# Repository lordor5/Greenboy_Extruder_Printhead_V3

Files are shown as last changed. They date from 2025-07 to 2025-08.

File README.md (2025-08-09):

# Greenboy_Extruder_Printhead_V3
An Alternative Printhead design for the Greenboy Pellet extruder

This toolhead brings many quality of life improvements like removable pellet hose connetor, easier assembly, more compact design, minimal disassembly required to pull the screw which can be performed with the printhead still attached to the printer and similar improvements.

As this design uses a seperate mounting plate between the printer and the printhead you only need to edit that to use it on a not yet supported printer, same with using another z probe for which there are 3 mounting holes in the mounting plate.

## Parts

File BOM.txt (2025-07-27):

Mandatory:

---------------------------------------------

Main body: 			4x m3x50
				4x m3 hexnut
		
Part cooling fan:		2x m3x18-20

Part cooling fan duct:		2x m3x6-10
				2x m3x6-10

Hotend cooling fan:		2x m3x18-20

Hotend cooling fan duct:	2x m3x6-10	

Mounting plate: 		3x m3x10
				3x m3 hexnut
---------------------------------------------

Mounting plate to printer:

---------------------------------------------

Ender 3:			2x m3x8

---------------------------------------------

Optional:

---------------------------------------------

Front bucket lid:		2x m3x8
				2x m3 hexnut

Z probe adapter BL-touch:	3x m3x8
				2x m3x6
				5x hexnut

Z probe adapter cartographer:	3x m3x10
	same as beacon rev-D	2x m3x8
				1x m3x20-25
				5x hexnut

---------------------------------------------

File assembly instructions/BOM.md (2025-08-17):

# Mandatory:

| Section | Fastener Type | Quantity |
| --- | --- | --- |
| **Main body** | m3x50 | 4 |
| | m3 hexnut | 4 |
| **Hotend fixture** | m4x8-12 | 4 |
| **Part cooling fan** | m3x18-20 | 2 |
| **Part cooling fan duct** | m3x6-10 | 4 |
| **Hotend cooling fan** | m3x18-20 | 2 |
| **Hotend cooling fan duct** | m3x6-10 | 2 |
| **Mounting plate** | m3x10 | 3 |
| | m3x8 | 2 |
| | m3 hexnut | 3 |
| | m3 7mm OD shims | 3 |
| **Front bucket lid** | m3x8 | 2 |
| | m3 hexnut | 2 |

---------------------------------------------

# Mounting plate to printer:

| Section | Fastener Type | Quantity |
| --- | --- | --- |
| Ender 3 | m3x8 | 2 |

---------------------------------------------

# Optional:

|Section|Fastener Type|Quantity|Notes|
|---|---|---|---|
|**Z probe adapter BL-touch**|m3x8|3||
||m3x6|2||
||hexnut|5||
|**Z probe adapter cartographer**|m3x10|3|Same as Beacon Rev-D|
||m3x8|2||
||m3x20-25|1||
||hexnut|5||

---------------------------------------------

If you notice any issues with this guide, have any questions or need clarifications
please contact me, preferably in the Greenboy3D discord @alx1234 or alternatively via email at alx.3dp@gmail.com

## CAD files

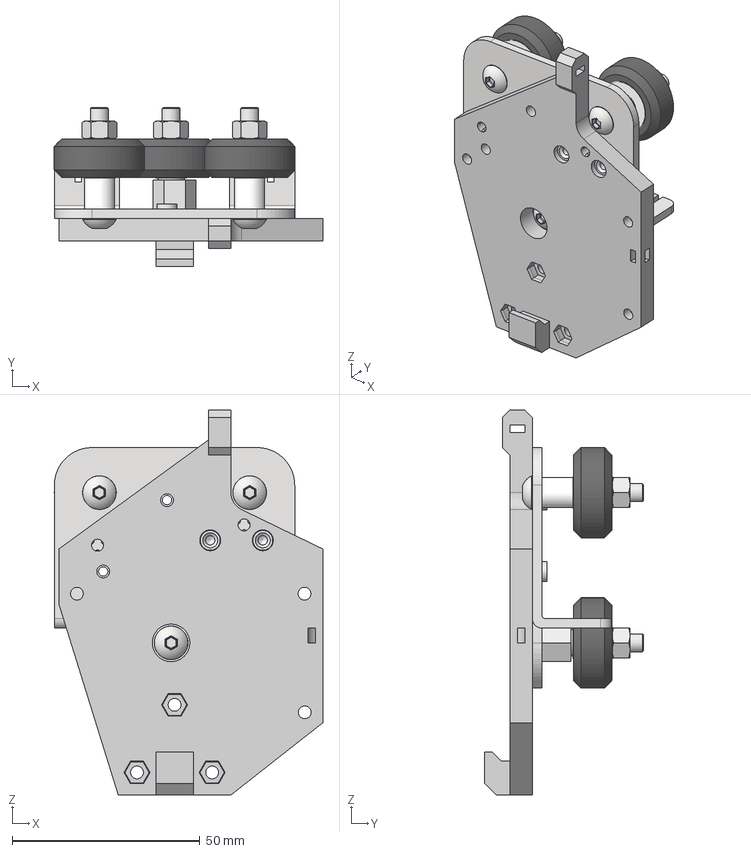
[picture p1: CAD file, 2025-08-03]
step/Mounting plates/Ender 3/Ender3 printer mounting plate.step
71.5 x 42.2 x 102.5 mm
Основание_3
AS 1112 - M5 Тип 5 x 3
Винт_1 x 3
Ролик_1 x 3
Эксцентрик
Дистанционная_ втулка x 2
GB printhead V3

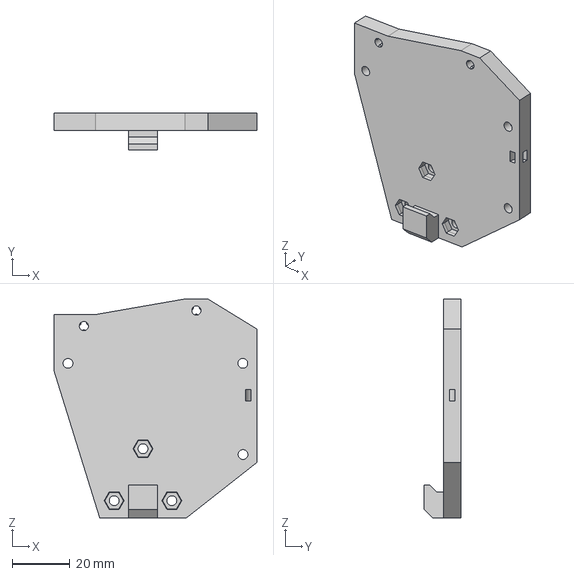
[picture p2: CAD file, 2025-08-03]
step/Mounting plates/mounting plate base.step
70.3 x 12.7 x 75.9 mm

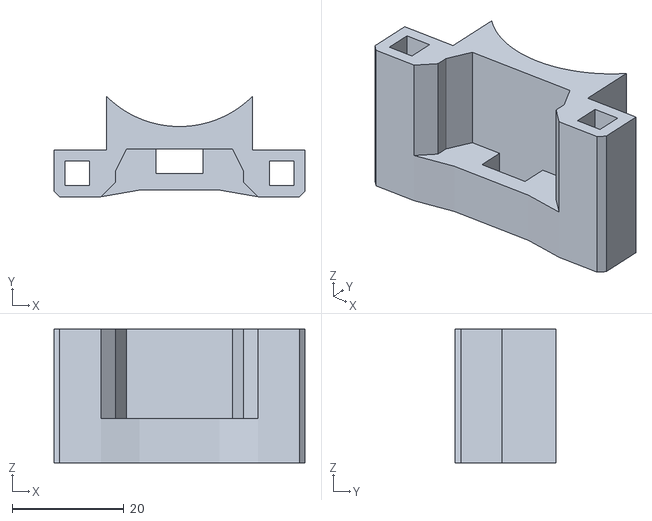
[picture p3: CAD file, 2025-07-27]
stl/alternate front/wall front.stl
45.0 x 18.0 x 24.0

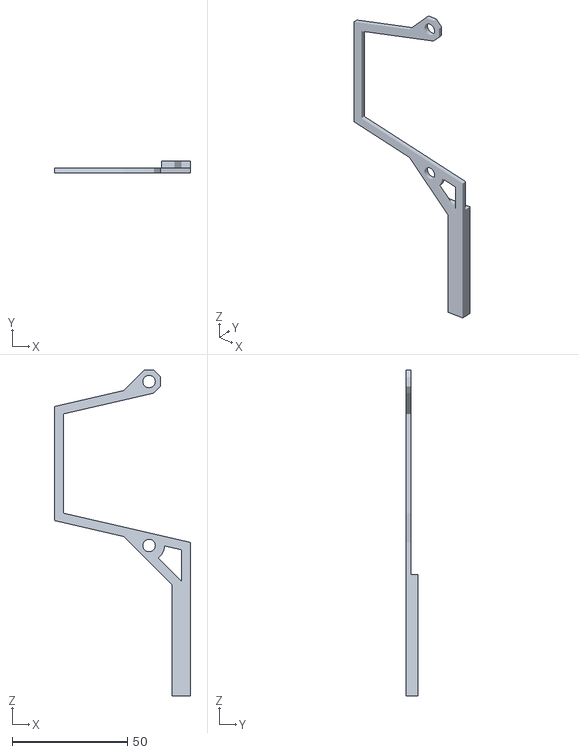
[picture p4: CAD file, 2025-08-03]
stl/Mounting plates/Ender 3/z limit switch extension.stl
59.0 x 5.00 x 141.1

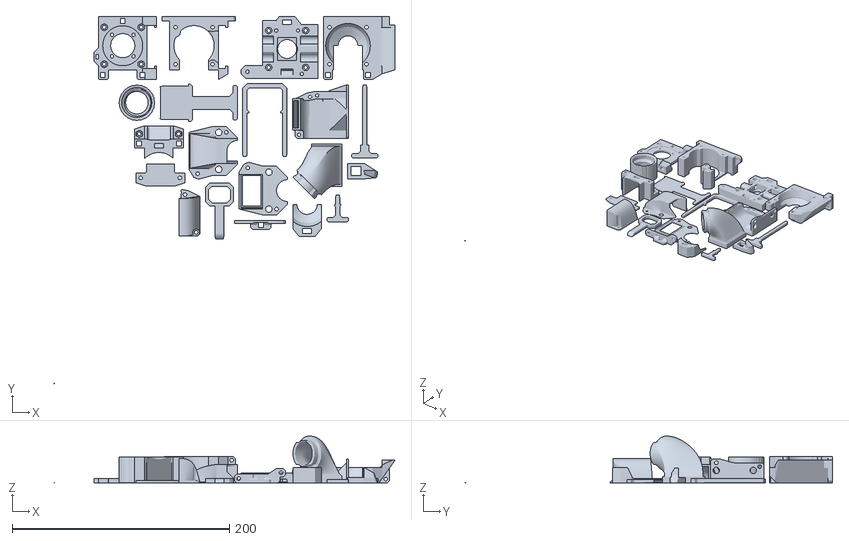
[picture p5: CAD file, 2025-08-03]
stl/Printhead all parts.stl
313.4 x 337.6 x 43.0

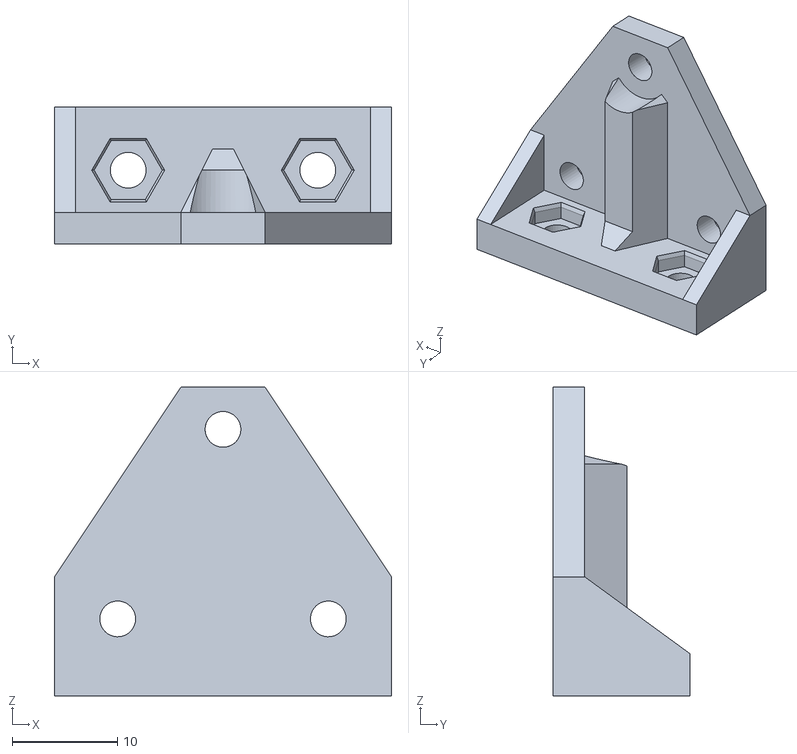
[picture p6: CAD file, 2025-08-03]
stl/z probe mounts/Bl touch mount.stl
32.0 x 13.0 x 29.3

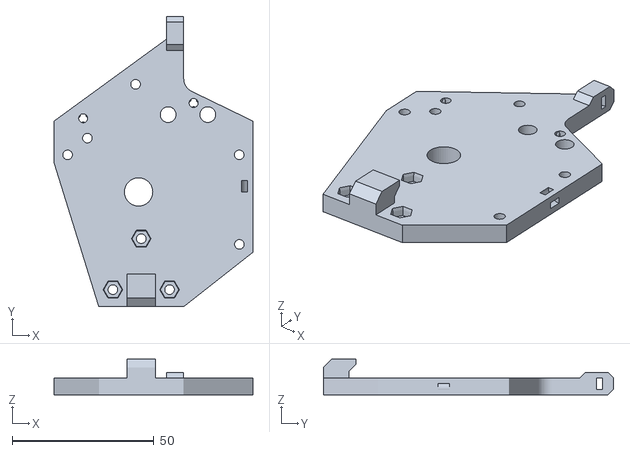
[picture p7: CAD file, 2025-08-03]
stl/Mounting plates/Ender 3/mounting plate Ender 3.stl
70.3 x 102.5 x 12.7

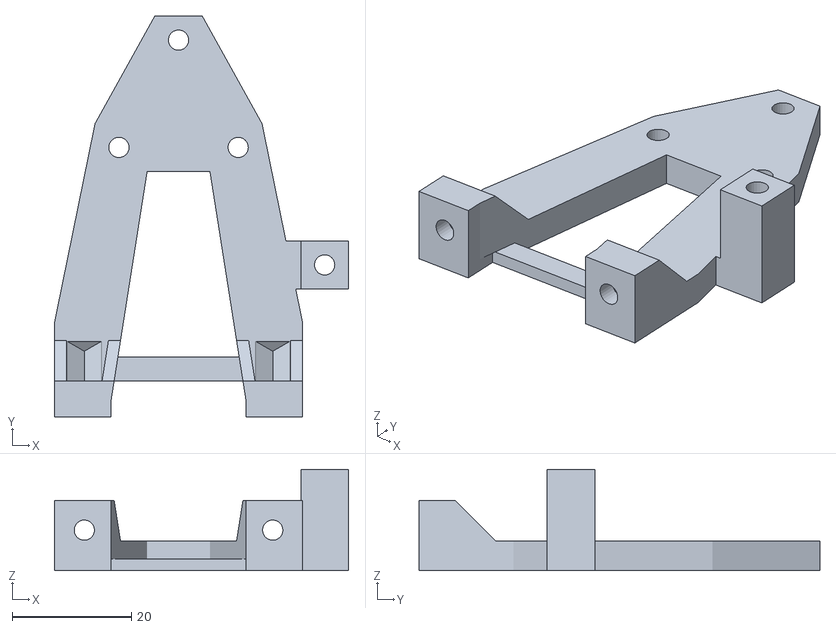
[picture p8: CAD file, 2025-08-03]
stl/z probe mounts/cartographer mount.stl
49.3 x 67.2 x 17.0

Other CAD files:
step/Mounting plates/Ender 3/Ender 3 z limit switch extension.step

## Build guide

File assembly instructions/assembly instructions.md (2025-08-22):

# Preparation:

Remove the old toolhead from the printer.

Use a m3 screw to drag the m3 hex nuts into their fixtures.
If you do not use a z probe you do not need the 3 bottom ones in the mounting plate

Assemble the Hotend by inserting the heater and thermistor into the heating block.
Screw the Heating block onto the Extruder barrel. If it is at a weird angle you can turn it around ans crew it on the other way. If the grub screws need to be on the bottom to have it align properly you can cut a bit of the insulation of the thermistor away to push it in further. Be careful not to cut the wires though.
You can screw in the nozzle at this point though that can also be done once its fully assembled.

Press the Inlet Rotor on top of the Pellet screw as far down as possible.
Make sure it is aligned right next to the inlet.
After that you can already put the coupler on the screw and tighten it down as much as possible.
I suggest getting some torx screws to allow better tightening without stripping the screw.
The coupler uses m2.5x8 screws.

Press the Pellet hose connector on the pellet hose adapter.
If your pellet hose is already the correct size you can also screw the pellet hose connector on it already, but you can also wait till the whole printhead is assembled.

# Assembly:

You can use the pictures in the pics folder for reference.

1. **Step one:** Screw the Motor plate to the Motor with 4 m3x6-8 screws.
Make sure you have the motor oriented the way you want it as you will not be able to chnage this later.

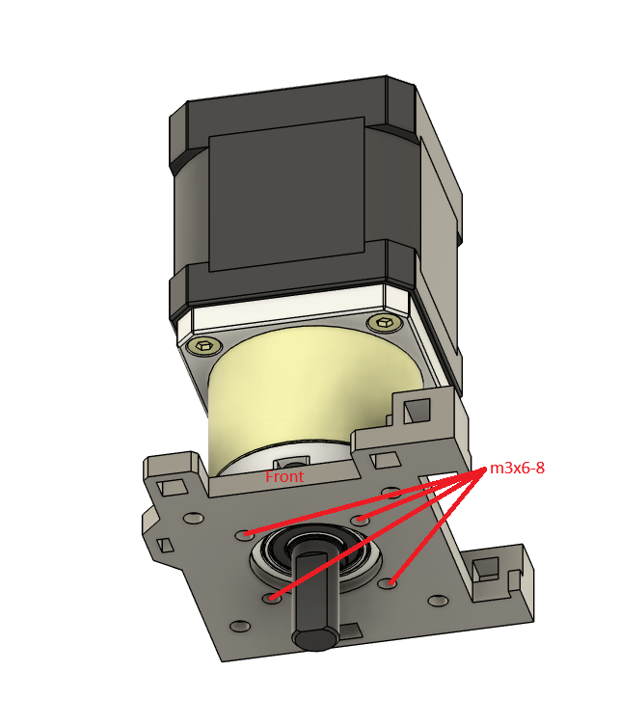
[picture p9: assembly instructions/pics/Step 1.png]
Step 1.png


2. **Step two:** Screw the Hotend Barrel into the Hotend fixture with 4 m4x8-12 screws.
Make sure the heating block is pointing backwards.
You might need to screpe a bit of material out of the printed part to fit the hotend properly.
Look through the holes of the Fixture to lighn the holes upproperly.
Be carful when screwing the scrws in to make sure everything is aligned properly so that you do not damage the threads of the Barrel.

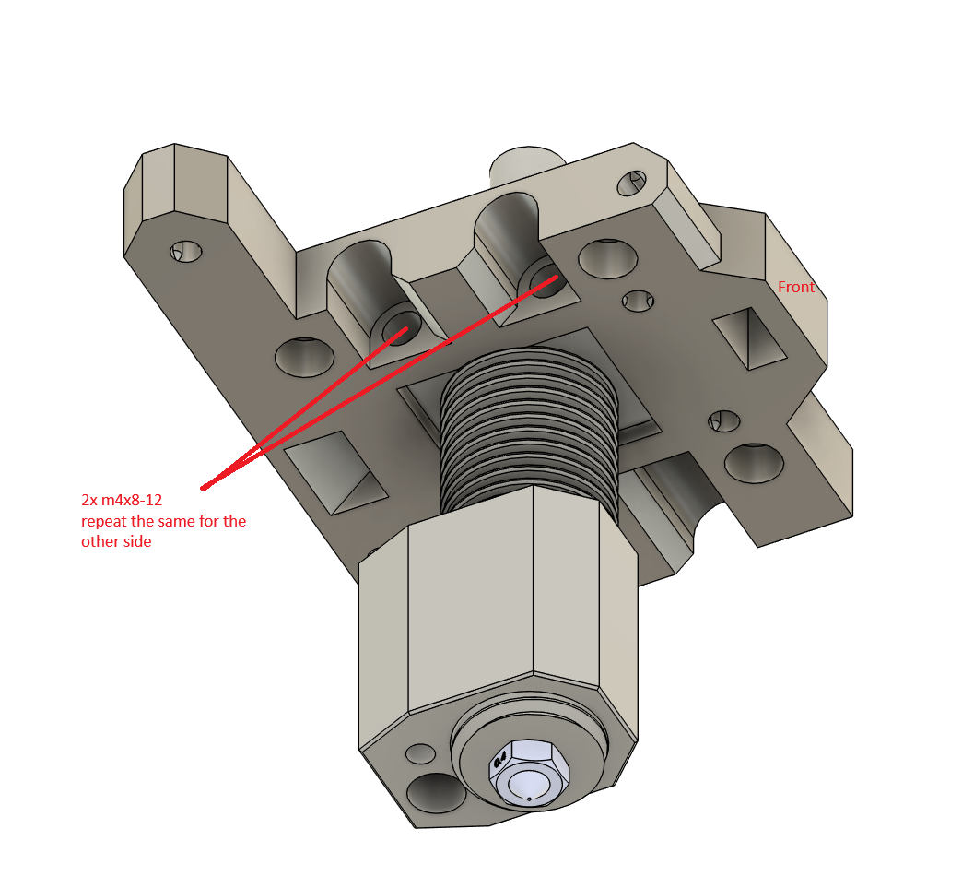
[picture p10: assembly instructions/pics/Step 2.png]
Step 2.png


3. **Step three:** Put the pellet screw in the hotend barrel. You need to have the rotor facing the front for this.
Use 4 m3x50 screws to connect the hotend fixture to the funnel,
pellet reservoir and motor plate and tighten them down.
Tighten the motor side of the coupler as much as you can, as said earlier.
I recommend getting torx screws to not have an issue with stripping them.

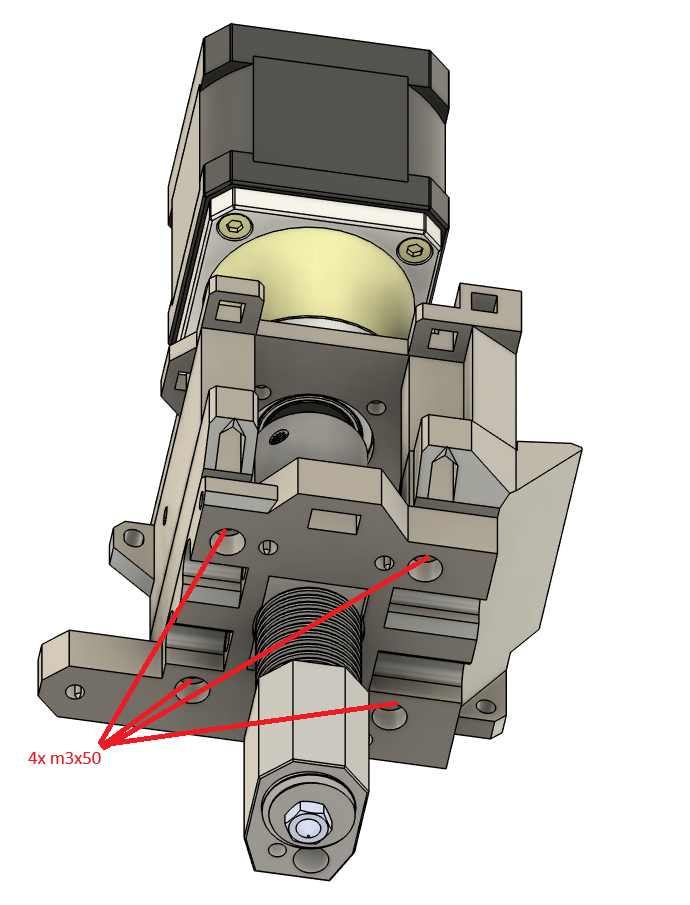
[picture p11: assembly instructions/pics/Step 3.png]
Step 3.png


4. **Step four:** Use 2 m3x18-20 screws to moun theHotend fan to the left side of the printhead.

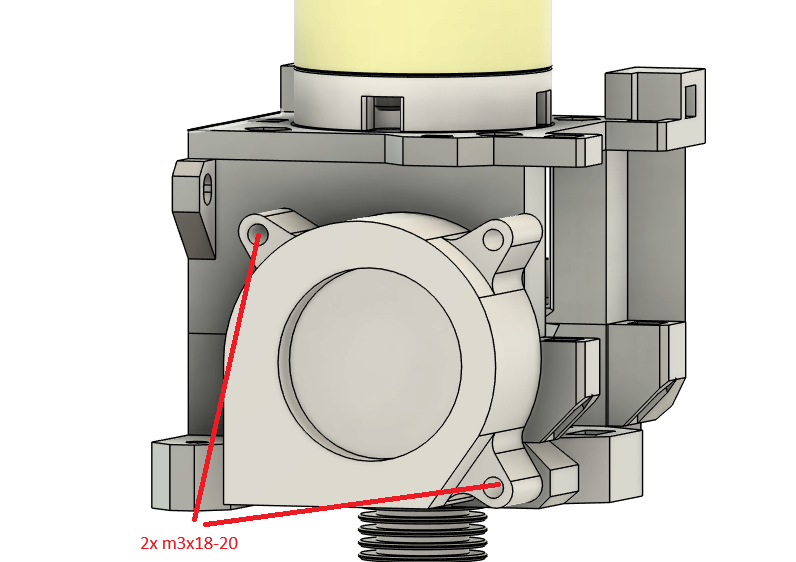
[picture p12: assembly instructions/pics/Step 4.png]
Step 4.png


5. **Step five:** Mount the 2 parts of the hotend cooling duct to the Printhead using 2 m3x6-10 screws.

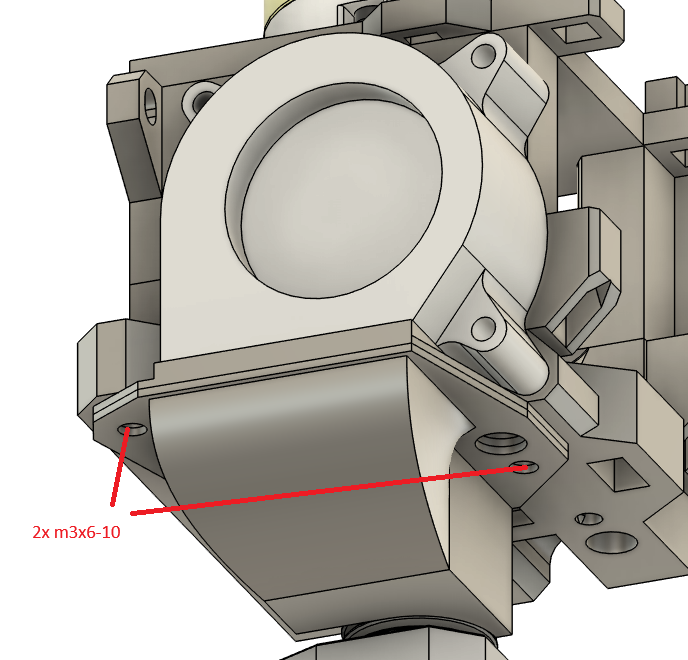
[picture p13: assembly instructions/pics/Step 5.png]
Step 5.png


6. **Step six:** Connect the 2 parts of the Part cooling duct with 2 m3x6-10 screws

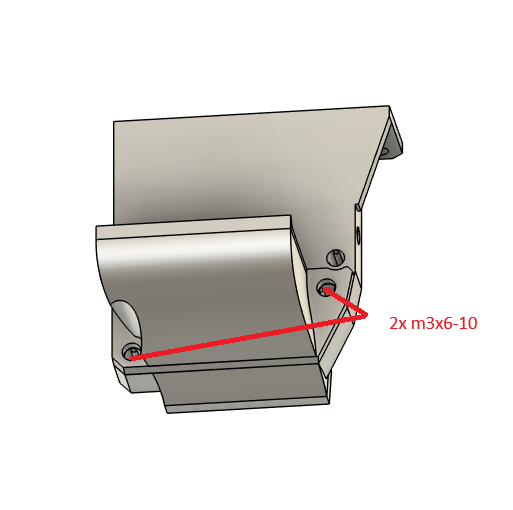
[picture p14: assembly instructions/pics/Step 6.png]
Step 6.png


7. **Step seven:** Mount the part cooling duct on the printhead woth 2 m3x6-10 screws.

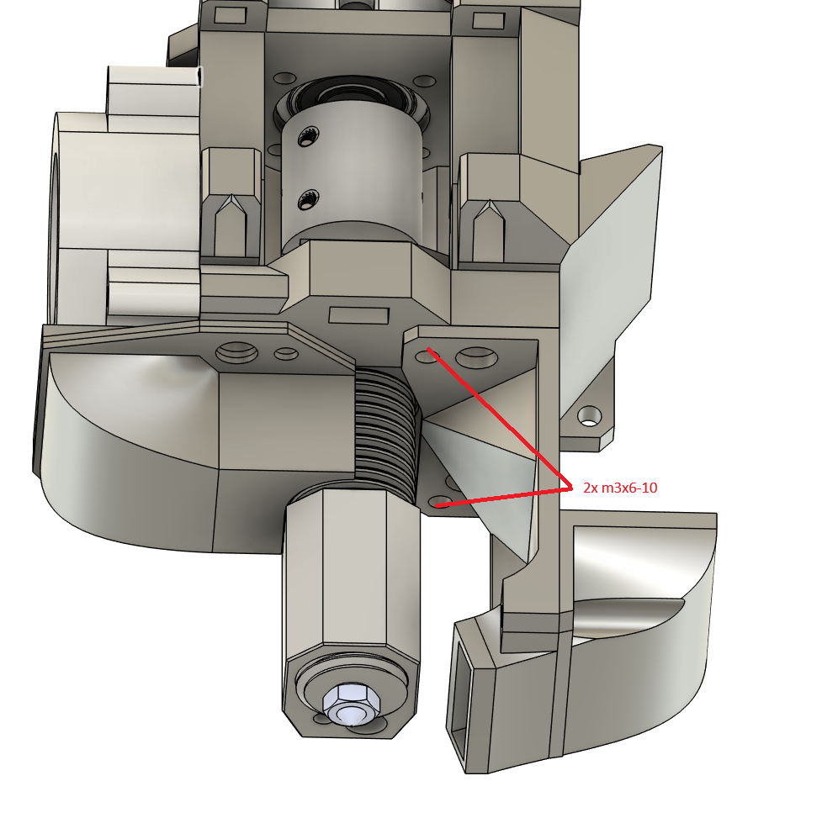
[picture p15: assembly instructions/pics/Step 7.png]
Step 7.png


8. **Step eight:** Screw the part cooling fan to the Printhead with 3 m3x18-20 screws.

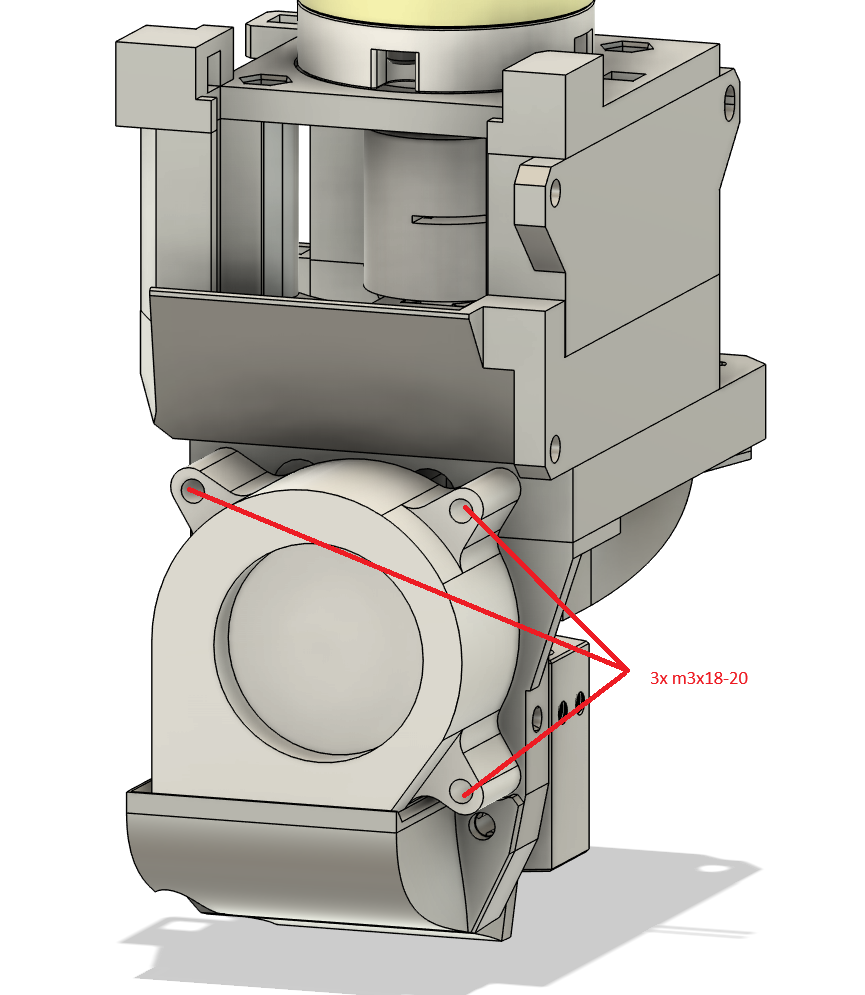
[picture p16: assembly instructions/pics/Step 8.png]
Step 8.png


9. **Step nine:** Screw the back latch fixture to the mounting plate with 2 m3x8 srew

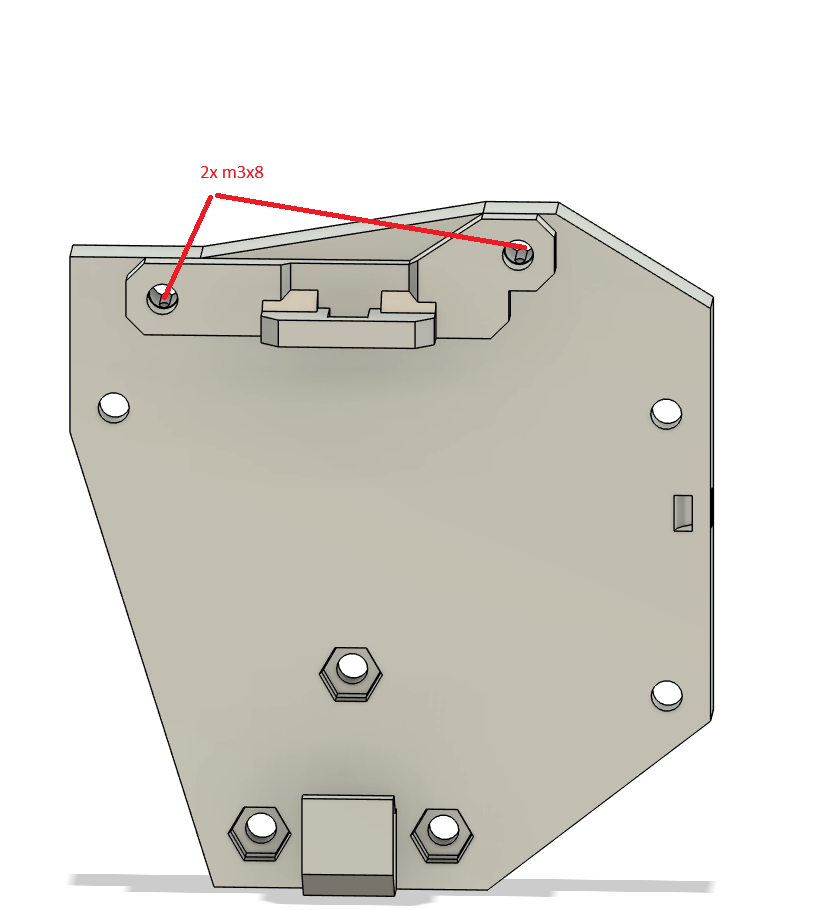
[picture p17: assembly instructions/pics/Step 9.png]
Step 9.png


10. **Step ten:** If you are using a z probe mount the Z-probe to the Z-probe mount and screw it to the mounting plate.
There are different screws used for this, consult the BOM to find out wich ones you need.

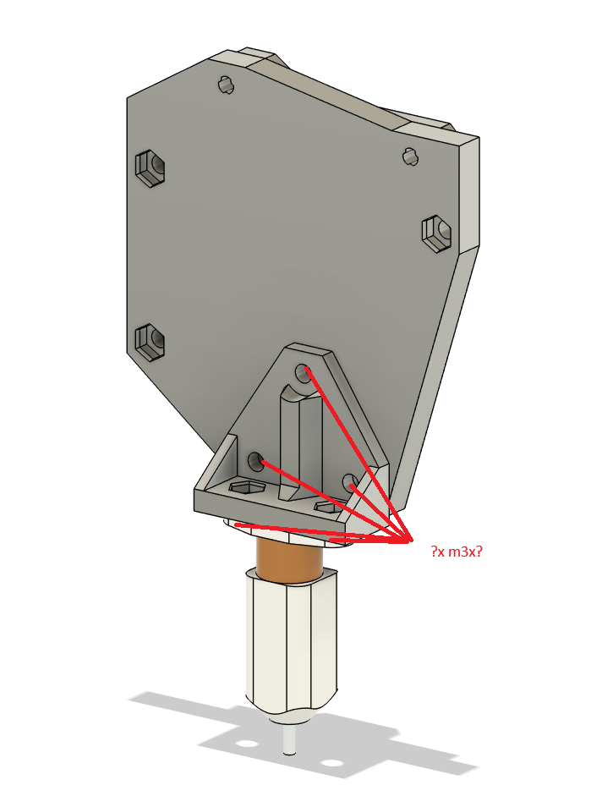
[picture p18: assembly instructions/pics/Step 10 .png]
Step 10.png


11. **Step eleven:** Mount the Mounting plate to the printhead.
Depending on your printer this needs different screws, consult the BOM for this.

12. **Step twelve:** Mount the printhead to the mounting plate.
Set it on the bottom hook first and then rotate it back flat onto the mounting plate.
secure it in theis position with the back latch.

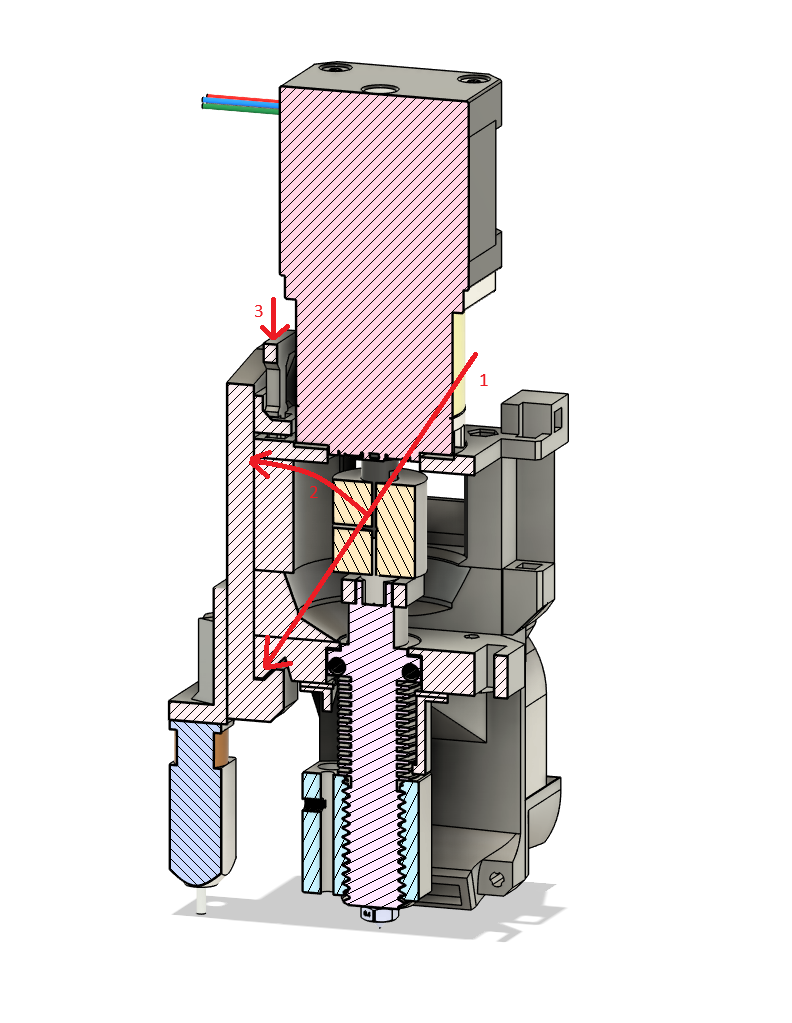
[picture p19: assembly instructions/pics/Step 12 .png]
Step 12.png


13. **Step thirteen:** Screw the printhead to the mounting plate with 3 m3x10 screws.
You should use shims for these screws to not damage the printed parts.
After this step you can remove the back latch and the back latch fixture.
This allows you to pull out the screw with the motor and motor plate
without completely disassembling the printhead.
You just loosen the 4 m3x5 screws from the bottom until they are pulled out of the motor plate.
Then you can lift the motor up while the hotend is hot.
if there is material in the screw pull it out as fast as possible as the molten plastics otherwise
can cool down in the cold zone of the extruder barrel causing the screw to get stuck.

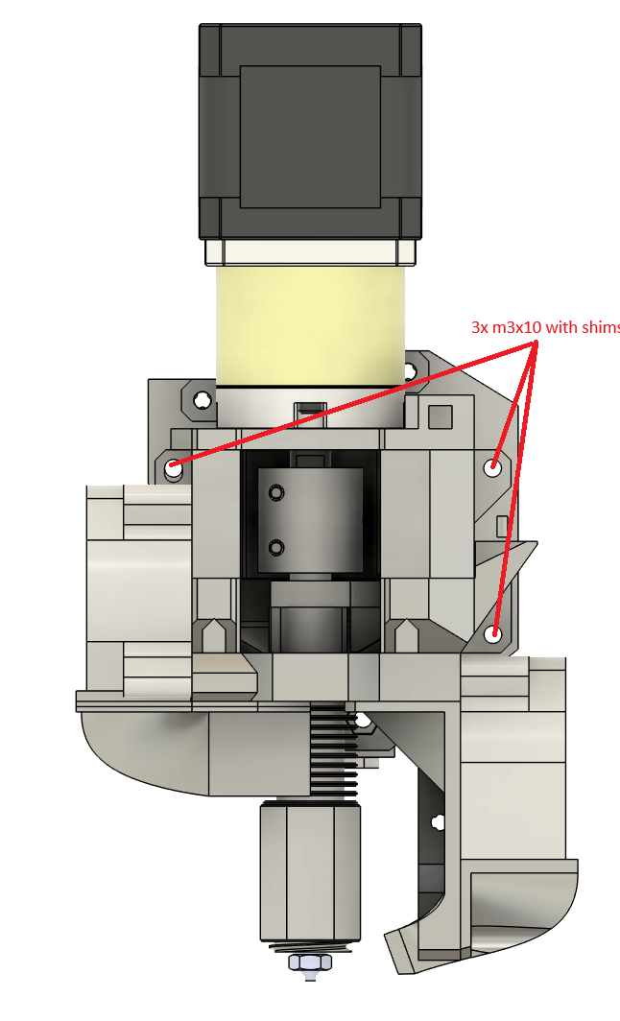
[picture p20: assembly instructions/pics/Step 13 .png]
Step 13.png


14. **Step fourteen:** First insert the bottom front and bucket front parts into the hole on the front of the printhead.
Then secure them with the lower and upper front latches.
If you need a lot of force to push the latches in sand them down a bit first.
You can also screw the bucket lid on the bucket front at this point if you want.
You can also wait until just befor or during the first print so that you can directly look at the screw.

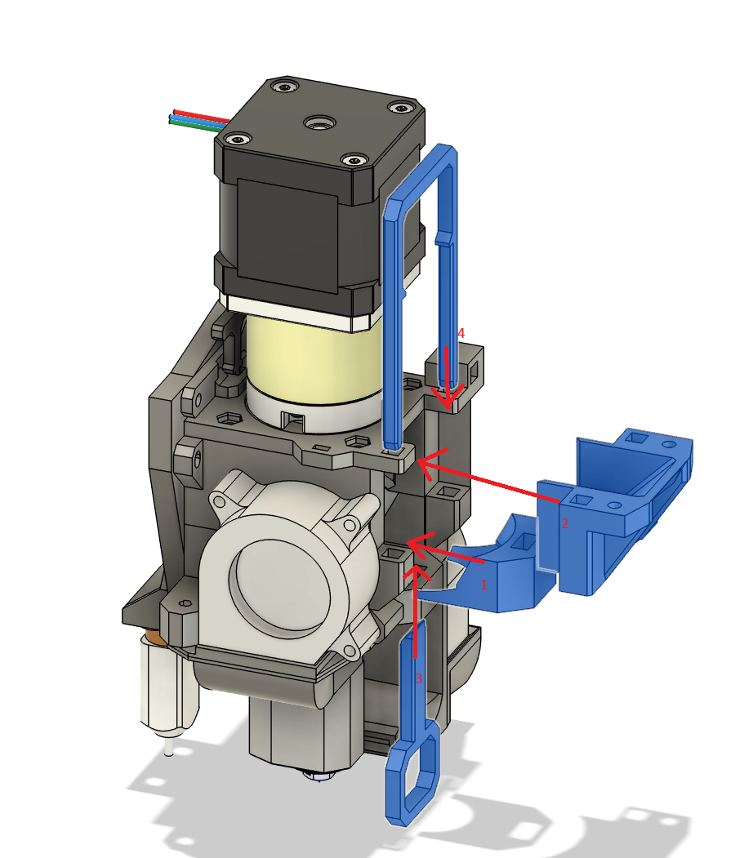
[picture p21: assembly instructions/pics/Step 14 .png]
Step 14.png


15. **Step fifteen:** Insert the Pellet hose connector into its place on the right side of the printhead.
After that secure it with the top latch.
Be careful to not use too much force for this.
Consider sanding it down istead as the holes in the motor plate are one of the weakest parts on the printhead.

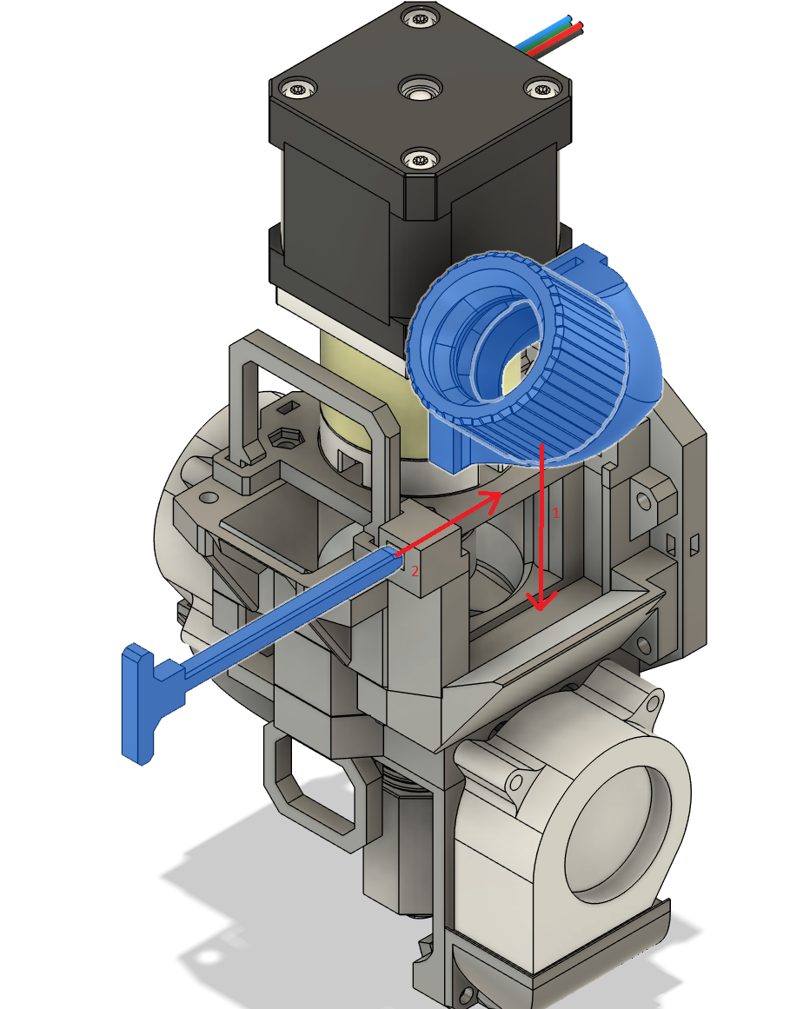
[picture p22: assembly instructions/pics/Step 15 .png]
Step 15.png


---
Congrats! The printhead is now fully assembled!

If you notice any issues with this guide, have any questions or need clarifications
please contact me, preferably in the Greenboy3D discord @alx1234 or alternatively via email at alx.3dp@gmail.com

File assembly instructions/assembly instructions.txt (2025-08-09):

Preparation:
------------
Remove the old toolhead from the printer.

Use a m3 screw to drag the m3 hex nuts into their fixtures.
If you do not use a z probe you do not need the 3 bottom ones in the mounting plate

Assemble the Hotend by inserting the heater and thermistor into the heating block.
Screw the Heating block onto the Extruder barrel. If it is at a weird angle you can turn it around ans crew it on the other way. If the grub screws need to be on the bottom to have it align properly you can cut a bit of the insulation of the thermistor away to push it in further. Be careful not to cut the wires though.
You can screw in the nozzle at this point though that can also be done once its fully assembled.

Press the Inlet Rotor on top of the Pellet screw as far down as possible.
Make sure it is aligned right next to the inlet. 
After that you can already put the coupler on the screw and tighten it down as much as possible.
I suggest getting some torx screws to allow better tightening without stripping the screw.
The coupler uses m2.5x8 screws.

Press the Pellet hose connector on the pellet hose adapter.
If your pellet hose is already the correct size you can also screw the pellet hose connector on it already, but you can also wait till the whole printhead is assembled.

Assembly: 
------------
You can use the pictures in the pics folder for reference. 

Step one: 	Screw the Motor plate to the Motor with 4 m3x6-8 screws.
		Make sure you have the motor oriented the way you want it as you will not be able to chnage this later.

Step two: 	Screw the Hotend Barrel into the Hotend fixture with 4 m4x8-12 screws.
		Make sure the heating block is pointing backwards.
		You might need to screpe a bit of material out of the printed part to fit the hotend properly.
		Look through the holes of the Fixture to lighn the holes upproperly.
		Be carful when screwing the scrws in to make sure everything is aligned properly so that you do not damage the threads of the Barrel.

Step three: 	Put the pellet screw in the hotend barrel. You need to have the rotor facing the front for this.
		Use 4 m3x50 screws to connect the hotend fixture to the funnel, 
		pellet reservoir and motor plate and tighten them down.
		Tighten the motor side of the coupler as much as you can, as said earlier. 
		I recommend getting torx screws to not have an issue with stripping them.

Step four:	Use 2 m3x18-20 screws to moun theHotend fan to the left side of the printhead.

Step five:	Mount the 2 parts of the hotend cooling duct to the Printhead using 2 m3x6-10 screws.

Step six:	Connect the 2 parts of the Part cooling duct with 2 m3x6-10 screws

Step seven:	Mount the part cooling duct on the printhead woth 2 m3x6-10 screws.

Step eight:	Screw the part cooling fan to the Printhead with 3 m3x18-20 screws.

Step nine: 	Screw the back latch fixture to the mounting plate with 2 m3x8 srew

Step ten:	If you are using a z probe mount the Z-probe to the Z-probe mount and screw it to the mounting plate.
		There are different screws used for this, consult the BOM to find out wich ones you need.

Step eleven:	Mount the Mounting plate to the printhead. 
		Depending on your printer this needs different screws, consult the BOM for this.

Step twelve:	Mount the printhead to the mounting plate.
		Set it on the bottom hook first and then rotate it back flat onto the mounting plate.
		secure it in theis position with the back latch.

Step thirteen:	Screw the printhead to the mounting plate with 3 m3x10 screws.
		You should use shims for these screws to not damage the printed parts.
		After this step you can remove the back latch and the back latch fixture.
		This allows you to pull out the screw with the motor and motor plate 
		without completely disassembling the printhead.
		You just loosen the 4 m3x5 screws from the bottom until they are pulled out of the motor plate. 
		Then you can lift the motor up while the hotend is hot.
		if there is material in the screw pull it out as fast as possible as the molten plastics otherwise 
		can cool down in the cold zone of the extruder barrel causing the screw to get stuck.

Step fourteen:	First insert the bottom front and bucket front parts into the hole on the front of the printhead.
		Then secure them with the lower and upper front latches. 
		If you need a lot of force to push the latches in sand them down a bit first.
		You can also screw the bucket lid on the bucket front at this point if you want. 
		You can also wait until just befor or during the first print so that you can directly look at the screw.

Step fifteen:	Insert the Pellet hose connector into its place on the right side of the printhead.
		After that secure it with the top latch. 
		Be careful to not use too much force for this.
		Consider sanding it down istead as the holes in the motor plate are one of the weakest parts on the printhead.

Congrats! The printhead is now fully assembled!

If you notice any issues with this guide, have any questions or need clarifications
please contact me, preferably in the Greenboy3D discord @alx1234 or alternatively via email at alx.3dp@gmail.com

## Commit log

2025-07-25 Add existing file
    [Ender 3 z limit switch extension.step, Ender3 printer mounting plate.step, mounting plate base.step]
2025-08-17 Update assembly instructions.md
2025-08-17 adding spacers
